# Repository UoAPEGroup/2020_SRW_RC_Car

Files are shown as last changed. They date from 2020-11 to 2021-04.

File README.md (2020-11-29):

# 2020 Summer Camp

- This repo contains work done by the students participating in the 2020 summer workshop, a voluntary summer internship program at UoA
- The students work on a project to design and build a wirelessly powered RC car
- The specifications for the design are (to be refined during the project)

| Parameter | Specification |
| --- | --- |
| Primary Supply | 50 V |
| IPT Frequency | 150 kHz |
| Rated Power | 50 W |
| Primary Compensation | LCL |
| Track Section Length | 1000 mm |
| Track Width | 300 mm |
| Lateral Tolerance | 50 mm |
| Max Change in k | 25% |
| Max Motor Voltage | 10 V |
| Max Steering Voltage | 5 V |
| Min Running Voltage  | 5 V |

- Work division is 
    - Power converter of the primary side IPT system: Sean McKeown & Henry Mitchell-Hibbert  
    - Embedded controller of the primary IPT system: Andrey Chukhraev & Isabelle Johns
    - Magnetic design of the primary side IPT coil: Arathi Biju & Alec Paton & Dexter Pham
    - Power converter of the vehicle side motor driver: Kimsong Lor  & Callum McDowell
    - Embedded controller of the vehicle side motor driver: Earlene Starling Babette & Raining Xing
    - Remote controller and steering controller of the vehicle: Neil Patil & Harris Tomy
    - Power converter of the vehicle side IPT system: Manoj Kumaraguru & Pranav Gulati

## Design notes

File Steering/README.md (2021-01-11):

# Design of the Remote and Steering Controllers

- Bluetooth Module 1R1 is located in `Steering/Hardware/Bluetooth_Module`
- Remote Controller 1R3 is located in `Steering/Hardware/Remote_Controller`
- Steering Converter 1R2 is located in `Steering/Hardware/Steering/Steering_Converter_1R2`

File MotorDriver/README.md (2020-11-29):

# Design of the Motor Driver

- Keep this document updated as you go

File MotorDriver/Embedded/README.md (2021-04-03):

# Motor Driver Embedded Side

The motor side embedded firmware controls the speed of the remote-controlled car by using PWM waves and an H-Bridge to variate the average voltage seen across the DC motor. Voltage at the H-Bridge, current at the H-Bridge, and motor power consumption data is sent to a live-updating website using BLE (bluetooth low energy) and an online PostGreSQL database. Safety features force the car to stop on over-voltage, over-current, and lost remote connection conditions.

## Features
- Uses an Atemga328PB to set the speed of the car between four set speeds [defined as STOP, MIN, MID, and MAX]
- Uses unipolar PWM modulation to change the duty cycle of PWM waves controlling the FETs in the H-Bridge
- Ramps voltage across motor at increments of 10 mV to prevent current spikes
- Switching frequency is 1.875kh
- Three safety paramaters cause the car to stop moving when triggered (at voltage > 20 V, current > 3 A, and if conenction to the remote controller team is lost)
- Connected to live-updating (voltage, current, and power data) website using BLE, python, and an online PostGreSQL database. See documentation here: link to software

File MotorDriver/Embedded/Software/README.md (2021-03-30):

# Live-updating Website

This website presents the H-Bridge voltage, H-Bridge current, and power through the wirelessly powered RC car through live-updating graphs. It also indicates the speed range (STOP, MIN, MID, MAX), direction (FORWARD, REVERSE), and which safety parameters (over voltage, over current, lost remote connection) are currently triggered.

website demo

## Features

* Graphs update live-time data relating to the voltage, current, and power of the car (speed is to be implemented)
* Indicates which safety parameter is triggered through button colors (red means that safety is triggered and that the car is stopped)
* Can be updated via bluetooth connection or serial connection to uController (note: serial connection is primarily used for testing)

## Documentation 

A local script (checkNearbyBLE.py) is used to find nearby BLE devices and print out their UUID numbers. 

The upstream script (updateDatabaseBL.py) reads incoming data from the microcontroller on the motor driver PCB. It then updates a PostGreSQL databse hosted on Heroku. This can be done sans bluetooth and with serial connection through (updateDatabseSerial.py).

A downstream script (bluetooth.py) periodically checks for updates in the databse. It generates the webpage and reflects any changes onto the graphs.

The webpage uses the Flask framework and is deployed via Heroku. 

## Key python libraries used: 

* Dash
* Plotly
* Bleak
* Psycopg2
* Asyncio
* Gunicorn
* Serial

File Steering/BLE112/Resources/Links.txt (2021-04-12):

BGSript VScode:
https://marketplace.visualstudio.com/items?itemName=SzczepanMejer.bgscript-support

https://www.digikey.com/eewiki/display/Wireless/Getting+Started+with+the+BlueGiga+BLE112+Bluetooth+Low+Energy+module
https://www.silabs.com/community/wireless/bluetooth/knowledge-base.entry.html/2015/08/06/_how-to_update_the-saZT

https://github.com/slackhappy/ble112/tree/master/serial_debug
https://sureshjoshi.com/embedded/bled112-virtual-com-stops-working/
https://github.com/CANBus-Triple/CBT-BLE112-Firmware
https://github.com/kilianc/iBeacon
https://github.com/sureshjoshi/ble113-firmware-examples

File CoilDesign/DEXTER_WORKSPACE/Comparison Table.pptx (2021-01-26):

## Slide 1

- # Ferrite Bars

- k_max (x = 0 mm, y = 50 mm)

- Minimum Power Output

- Maximum Power Output

- k_min (x = mid, y = 50 mm)

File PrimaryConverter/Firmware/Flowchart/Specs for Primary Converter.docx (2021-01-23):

Important specifications:

- System clock = 8MHz
- ADC resolution = 10-bit
- ADC clock = 250kHz
- ADC sampling every 1us using Timer/Counter1(16-bit) CTC comp_B (needs check)
- ADC sampling size = 10 readings per channel
- ADC reference voltage = AVCC = 3.3V
- USART0 – 8N1 – no parity
- Baud rate = 9600 (standard)
- Transmitting data to terminal every 1s using Timer/Counter3(16-bit) OVF
- Timer/Counter0, 2 are used for PWM signal generation to control the drivers for the H-bridge

Work in progress:

- Implementing ramping down of the PWM signals for over voltage, current and temperature
- Determining communication protocols with the Bluetooth module

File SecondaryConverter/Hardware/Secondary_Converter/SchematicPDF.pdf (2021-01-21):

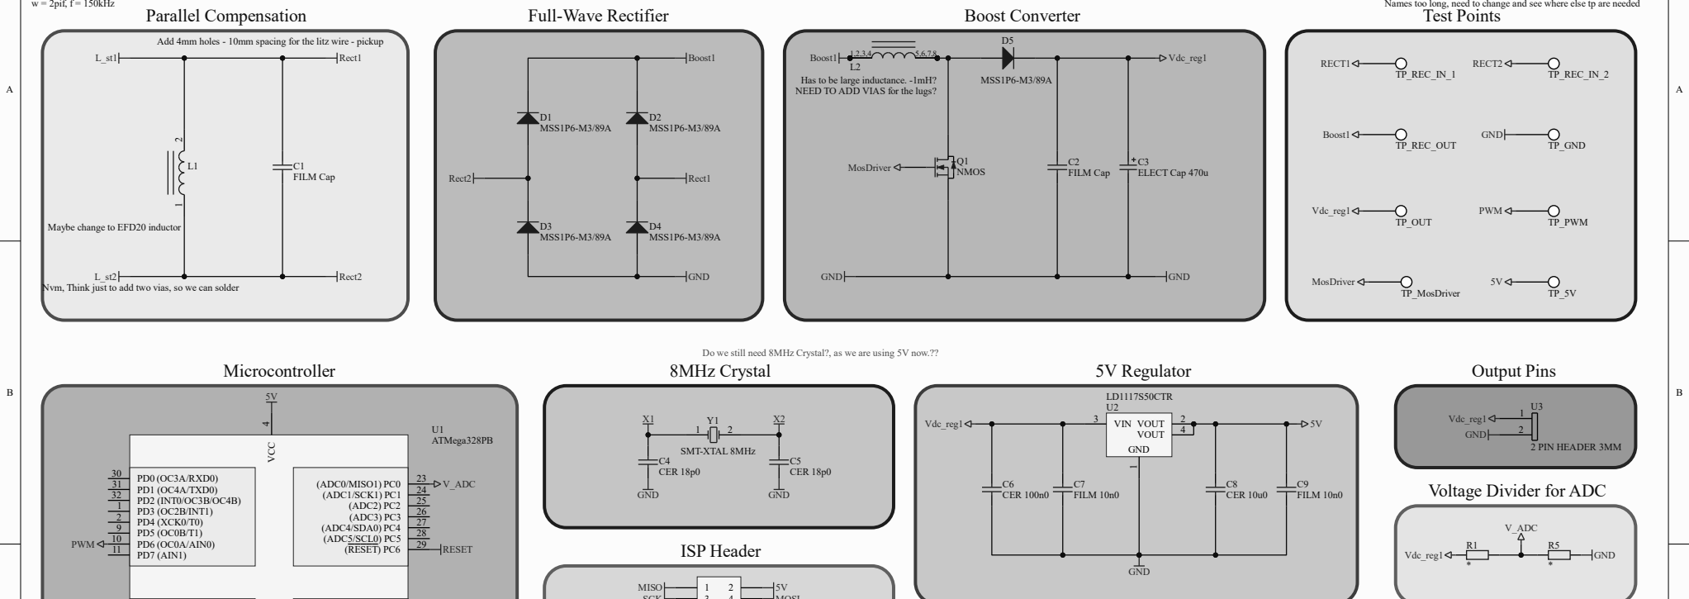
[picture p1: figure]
C1 FILM Cap; Rect1; Rect2; Parallel Compensation; D1 MSS1P6-M3/89A; D2 MSS1P6-M3/89A; D3 MSS1P6-M3/89A; D4 MSS1P6-M3/89A; Full-Wave Rectifier; Boost1; GND; MSS1P6-M3/89A; C2 FILM Cap; Vdc_reg1; Boost Converter 1 2; VCC; PD1 (OC4A/TXD0) 31 PD2 (INT0/OC3B/OC4B) 32 PD3 (OC2B/INT1) 1 PD4 (XCK0/T0) 2 PD5 (OC0B/T1) 9 PD6 (OC0A/AIN0) 10 PD7 (AIN1) 11; PD0 (OC3A/RXD0) 30; (ADC0/MISO1) PC0; (ADC1/SCK1) PC1; (ADC2) PC2; (ADC3) PC3; (ADC4/SDA0) PC4; (ADC5/SCL0) PC5; (RESET) PC6; U1 ATMega328PB; Q1 NMOS; NEED TO ADD VIAS for the lugs?; Has to be large inductance. -1mH?; TP_GND; TP_REC_IN_1; RECT1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
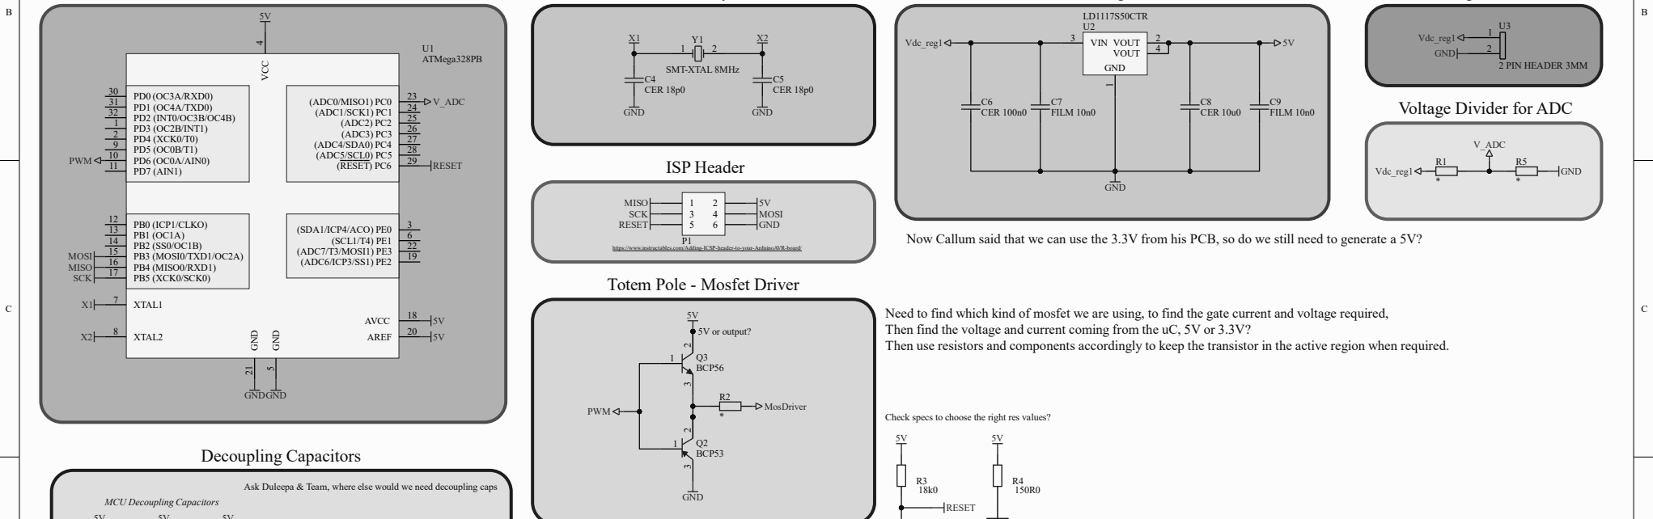
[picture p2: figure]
XTAL1 7; XTAL2 8; AVCC; AREF; PB5 (XCK0/SCK0) 17; PB0 (ICP1/CLKO) 12 PB1 (OC1A) 13 PB2 (SS0/OC1B) 14 PB3 (MOSI0/TXD1/OC2A) 15; PB4 (MISO0/RXD1) 16; (ADC6/ICP3/SS1) PE2; 19 (ADC7/T3/MOSI1) PE3; (SDA1/ICP4/ACO) PE0; (SCL1/T4) PE1; 6 GND; 5 GND 21; GNDGND; Decoupling Capacitors; SCK RESET; MOSI GND; https://www.instructables.com/Adding-ICSP-header-to-your-ArduinoAVR-board/; MISO SCK; MOSI; Q3 BCP56 2; Q2 BCP53; PWM; GND; 5V 5V or output?; MosDriver; Totem Pole - Mosfet Driver; MCU Decoupling Capacitors; RESET

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
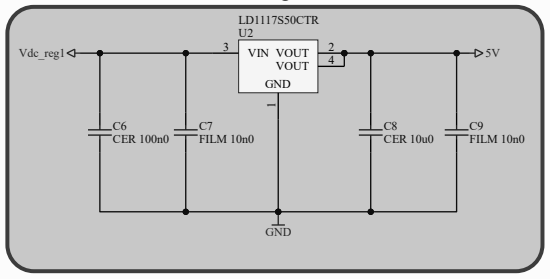
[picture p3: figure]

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
University Of Auckland
20 Symonds Street,
Auckland CBD,
Auckland 1010,

### 1 New Zealand

## Secondary Converter

1

21/01/2021 | 12:25:39 PM
C:\Users\Manoj\Documents\GitHub\2020-srw-rc-car\SecondaryConverter\Hardware\Secondary_Converter\IPT_Secondary_Converter.SchDoc

Title:

Author:
Date:
File:

Revision:
Time: | Sheet | of

### Pranav G & Manoj K

Note: Can only find the value of the capacitor after determing the value of the inducatnce As wL = 1/wC, C = 1/w^2*L
w = 2pif, f = 150kHz

Add 4mm holes - 10mm spacing for the litz wire - pickup

A Sinusoidal coil is used as the pick up, using parallel compensation to build the voltage and to achieve reasonance. Then the signal goes to the full-wave rectifier whcih transforms the ac voltage to dc voltage. The signal from the rectifiers goes to the boost converter.

Main Idea: As the pick up voltage is going to be a low AC voltage, need to convert this signal into a DC voltage and also boost up the voltage to 5-12V; ideally 10V.

Add regulator for 3v3/5v supply - possibly LD1117S50CTR . Add header for possible use by other teams. Add zener diode to protect regulator

# TO DO:

Do we still need 8MHz Crystal?, as we are using 5V now.??

C10
100n

C11
100n

C12
100n
GND | GND | GND
5V | 5V | 5V
C13
18n0

GND

GND

D6
Green

Input voltage in the range of 4-7V, maybe 3V, so for safety just keep it 3-8V. - Still need to confirm with Coil group

Now Callum said that we can use the 3.3V from his PCB, so do we still need to generate a 5V?

Need to find which kind of mosfet we are using, to find the gate current and voltage required,

## Then find the voltage and current coming from the uC, 5V or 3.3V?

Then use resistors and components accordingly to keep the transistor in the active region when required.

Ask Duleepa & Team, where else would we need decoupling caps

Check which type of diodes to use? Names too long, need to change and see where else tp are needed

Check specs to choose the right res values?

Nvm, Think just to add two vias, so we can solder

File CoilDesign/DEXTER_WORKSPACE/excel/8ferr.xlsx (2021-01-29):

Variation | $X_displacement | $Y_displacement | Lst_Wdg: Freq(150kHz): Matrix1 | k_Wdg: Freq(150kHz): Matrix1 | M_Wdg: Freq(150kHz): Matrix1 | L_pt_Wdg: Freq(150kHz): Matrix1
1 | 0mm | 0mm | 139.655626661595nH | 0.1221841069 | 216.627674501381nH | 22508.1603069312nH
2 | 0mm | 50mm | 139.491337467754nH | 0.08543539432 | 150.706136955698nH | 22306.8876871537nH
3 | 67.5mm | 0mm | 128.32776882356nH | 0.09409683698 | 159.205421658519nH | 22307.1975334523nH
4 | 67.5mm | 50mm | 128.399777350217nH | 0.06737563071 | 113.710914979nH | 22183.7187301038nH

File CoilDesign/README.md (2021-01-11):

# Design of the Primary and Secondary Couplers

FinalModel :
- Contains latest ansys model for project (no solution data to save space)

Analysis Results:
- Excel files exported from parametric sweep 3
- Graphs of k vs x and y displacement
- .xlsx file sheet 1 is password protected to avoid data corruption as sheet 2 is dependent on sheet 1 cell values
- password is abc123 (please do not change cell values without making backup)

- Update the .gitignore as needed to avoid storing solution files
- Keep this document updated as you go

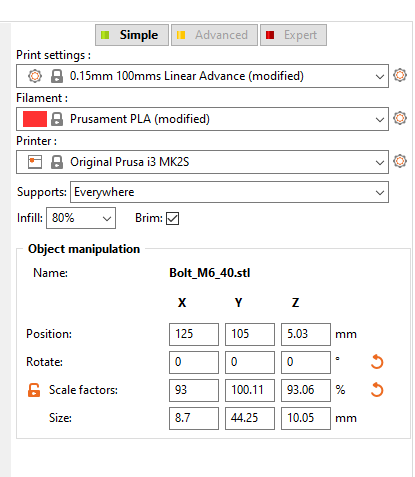
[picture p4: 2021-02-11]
CoilDesign/Arathi_Workspace/m6_40_settings.PNG

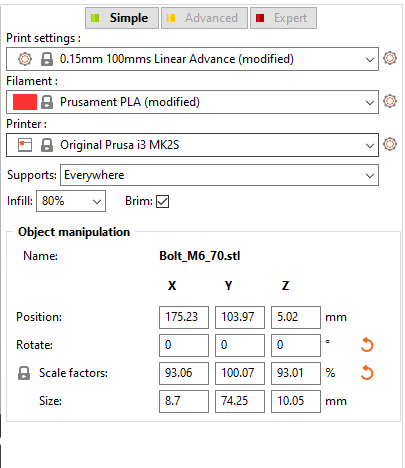
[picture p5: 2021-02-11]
CoilDesign/DEXTER_WORKSPACE/CONFIDENTIAL/m6_70_settings.PNG

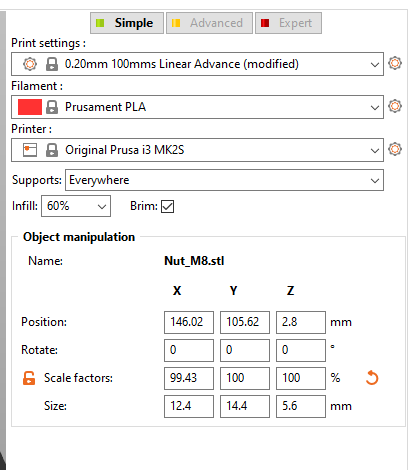
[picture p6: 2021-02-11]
CoilDesign/DEXTER_WORKSPACE/CONFIDENTIAL/m8_nut_settings.PNG

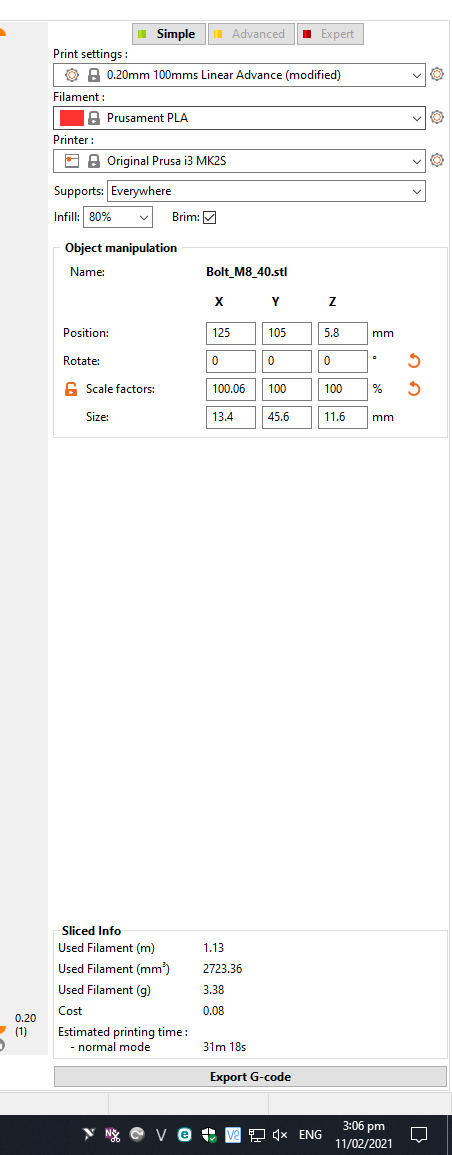
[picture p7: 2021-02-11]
CoilDesign/DEXTER_WORKSPACE/CONFIDENTIAL/m8_40_settings.PNG

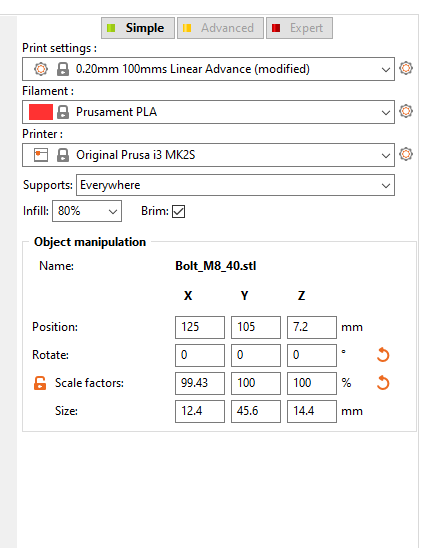
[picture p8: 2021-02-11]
CoilDesign/Arathi_Workspace/m8_40_settings.PNG

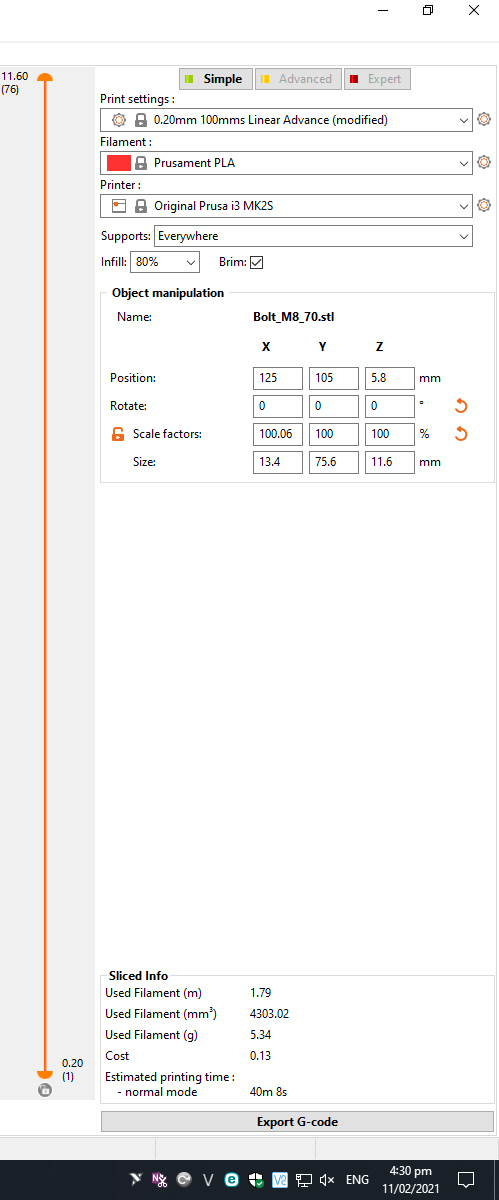
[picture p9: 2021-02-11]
CoilDesign/DEXTER_WORKSPACE/CONFIDENTIAL/m8_70_settings.PNG

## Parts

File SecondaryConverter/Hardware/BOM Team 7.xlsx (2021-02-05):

Index | Part Number | Supplier | Manufacturer Part Number | Description | QTY | QTY (Price Break) | Unit Cost (NZD) | Total Cost (NZD) | Unit PB Cost | Total PB Cost | Requester
1 | 445-7348-1-ND | Digikey | C1005X7R1E104K050BB | (Parallel Compensation) 0.1µF ±10% 25V Ceramic Capacitor X7R 0402 (1005 Metric) | 4 | 10 | 0.19 | 0.76 | 0.133 | 1.33 | Secondary
2 | SDT5H100P5-7DICT-ND | Digikey | SDT5H100P5 | Diode Schottky 100V 5A Surface Mount PowerDI™ 5 | 5 | 10 | 0.71 | 3.55 | 0.611 | 6.11 | Secondary
3 | BSC072N08NS5ATMA1CT-ND | Digikey | BSC072N08NS5ATMA1CT | N-Channel 80V 74A (Tc) 2.5W (Ta), 69W (Tc) Surface Mount PG-TDSON-8-7 | 1 | 10 | 2.72 | 2.72 | 2.228 | 22.28 | Secondary
4 | 1276-3387-1-ND | Digikey | CL32B106KBJNNNE | (Short-cct Reg Cap) 10µF ±10% 50V Ceramic Capacitor X7R 1210 (3225 Metric) | 1 | 10 | 0.88 | 0.88 | 0.623 | 6.23 | Secondary
5 | 36-5015CT-ND | Digikey | 5015 | PC Test Point, Miniature Phosphor Bronze, Silver Plating Surface Mount Mounting Type | 15 | 25 | 0.66 | 9.9 | 0.534 | 13.35 | Secondary & MotorDriver
6 | 1276-1003-1-ND | Digikey | CL21B104KBCNNNC | (Decoupling Caps) 0.1µF ±10% 50V Ceramic Capacitor X7R 0805 (2012 Metric) | 4 | 10 | 0.15 | 0.6 | 0.074 | 0.74 | Secondary
7 | 469-1027-ND | Digikey | 9027 | Magnet 1 | 3 | 5 | 0.62 | 1.86 | 0.592 | 2.96 | Raining
8 | 1835-M1219-1-ND | Digikey | M1219-1 | Magnet 2 | 3 | 5 | 0.89 | 3.89 | 0.852 | 4.26 | Raining
9 | AH374-W-7DICT-ND | Digikey | AH374-W-7 | Hall Effect Sensor | 3 | 10 | 1.02 | 3.06 | 0.89 | 8.9 | Raining
10 | 1470-4533-ND | Digikey | SRH05S12 | DC DC CONVERTER 12V | 2 | 5 | 12.34 | 24.68 | 11.972 | 59.86 | Primary
11 | 296-TMCS1100A3QDRCT-ND | Digikey | TMCS1100A3QDR | PRECISION ISOLATED CURRENT SENSOR | 3 | 10 | 6.5 | 19.5 | 5.83 | 58.3 | Primary
12 | 1470-2974-5-ND | Digikey | ISE0312A | DC DC CONVERTER 12V 1W | 1 | 5 | 6.79 | 6.79 | 6.36 | 31.8 | MotorDriver
13 | SMBJ5354B-TPMSCT-ND | Digikey | SMBJ5354B-TP | DIODE ZENER 17V 5W DO214AA | 1 | 10 | 0.63 | 0.63 | 0.544 | 5.44 | MotorDriver
14 | 1928-SMDTC04220TB00KQ00DKR-ND | Digkey | SMDTC04220TB00KQ00 | CAP FILM 2.2UF 10% 63VDC 2824 | 3 | 10 | 2.79 | 8.37 | 2.206 | 22.06 | MotorDriver
15 | 296-30207-ND | Digikey | CC-DEBUGGER | KIT DEBUGGER/PROGRAMMER | 1 | 1 | 90.72 | 90.72 | 90.72 | 90.72 | Duleepa <3
 |  |  |  |  |  |  |  | TOTAL PRICE (w/out PB) |  | TOTAL PRICE (w/ PB)
 |  |  |  |  |  |  |  | 177.91 |  | 334.34

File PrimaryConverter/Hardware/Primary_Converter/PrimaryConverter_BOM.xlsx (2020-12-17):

Steering Controller
Item # | Component | Description | Quantity | Price (Inc. GST) | Link | Notes
1 | EFD20/10/7-3C96 | FERRITE CORE | 4 | $1.45 | https://www.digikey.co.nz/product-detail/en/ferroxcube/EFD20-10-7-3C96/1779-1076-ND/7041536
2 | B66418W1008D001 | BOBBIN COIL FORMER EFD 20X10X7 | 2 | $2.31 | https://www.digikey.co.nz/product-detail/en/epcos-tdk-electronics/B66418W1008D001/495-5524-ND/3914936
3 | B66418B2000X000 | YOKE EFD 20 X 10 X 7 | 4 | $0.57 | https://www.digikey.co.nz/product-detail/en/epcos-tdk-electronics/B66418B2000X000/495-5523-ND/3915648
4 | BSC072N08NS5ATMA1 | MOSFET N-Ch 80V 74A TDSON-8 | 4 | $2.64 | https://nz.mouser.com/ProductDetail/Infineon-Technologies/BSC072N08NS5ATMA1/
5 | TMCS1100A2 | PRECISION ISOLATED CURRENT SENSOR | 1 | $3.98 | https://www.digikey.com/en/products/detail/texas-instruments/TMCS1100A2QDR/12696012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
6 | 8MHz Crystal | TXC CORP CRYSTAL 8.0000MHZ 18PF SMD | 1 | $0.67 | https://www.digikey.co.nz/product-detail/en/txc-corporation/9C-8-000MAAJ-T/887-1048-1-ND/2118925
7 | ATMEGA328PB-AU-ND | ATMEGA328PB-AU-ND | 1 | $1.34 | https://www.digikey.com/en/products/detail/microchip-technology/ATMEGA328PB-AU/5638812
8 | SRH05S12 | DC DC CONVERTER 12V | 1 | $12.79 | https://www.digikey.co.nz/products/en?keywords=srh05s12
9 | IRS21834SPBF | IC GATE DRVR HALF-BRIDGE 14SOIC | 2 | $4.83 | https://www.digikey.co.nz/product-detail/en/infineon-technologies/IRS21834SPBF/IRS21834SPBF-ND/1189739
10 | AP2210K-3.3TRG1 | IC REG LINEAR 3.3V 300MA SOT23-5 | 1 | $0.66 | https://www.digikey.co.nz/product-detail/en/diodes-incorporated/AP2210K-3-3TRG1/AP2210K-3-3TRG1DICT-ND/4505291
11 | MSS1P6-M3/89A | DIODE SCHOTTKY 60V 1A MICROSMP | 2 | $0.42 | https://www.digikey.co.nz/product-detail/en/vishay-semiconductor-diodes-division/MSS1P6-M3-89A/MSS1P6-M3-89AGICT-ND/2071763
12 | ECP-U1C104MA5 | CAP FILM 0.1UF 20% 16VDC 0805 | 7 | $0.91 | https://www.digikey.co.nz/product-detail/en/panasonic-electronic-components/ECP-U1C104MA5/PCF1126CT-ND/285453 | 0805 decoupling caps for 12V and down
13 | CGA5L2C0G1H104J160AA | CAP CER 0.1UF 50V C0G 1206 | 3 | $0.78 | https://www.digikey.co.nz/product-detail/en/tdk-corporation/CGA5L2C0G1H104J160AA/445-6984-1-ND/2673002 | 1206 decoupling caps for fet outer loop
14 | CL32B106KBJNNNE | CAP CER 10UF 50V X7R 1210 | 2 | $0.94 | https://www.digikey.co.nz/product-detail/en/samsung-electro-mechanics/CL32B106KBJNNNE/1276-3387-1-ND/3891473
15 | CL32B105KCJNNNE | CAP CER 1UF 100V X7R 1210 | 2 | $0.56 | https://www.digikey.co.nz/product-detail/en/samsung-electro-mechanics/CL32B105KCJNNNE/1276-1812-6-ND/3892326
16 | CL21B225KPFNNNE | CAP CER 2.2UF 10V X7R 0805 | 1 | $0.18 | https://www.digikey.co.nz/product-detail/en/samsung-electro-mechanics/CL21B225KPFNNNE/1276-1188-1-ND/3889274
17 | CL21B105KOFNNNG | CAP CER 1UF 16V X7R 0805 | 1 | $0.16 | https://www.digikey.co.nz/product-detail/en/samsung-electro-mechanics/CL21B105KOFNNNG/1276-6471-1-ND/5958099
18 | CL21C101JCANNNC | CAP CER 100PF 100V C0G/NP0 0805 | 1 | $0.16 | https://www.digikey.co.nz/product-detail/en/samsung-electro-mechanics/CL21C101JCANNNC/1276-1261-1-ND/3889347
19 | CL32B225KCJSNNE | CAP CER 2.2UF 100V X7R 1210 | 2 | $0.74 | https://www.digikey.co.nz/product-detail/en/samsung-electro-mechanics/CL32B225KCJSNNE/1276-3362-1-ND/3891448
20 | CL21C200JBANNNC | CAP CER 20PF 50V C0G/NP0 0805 | 2 | $0.16 | https://www.digikey.co.nz/product-detail/en/samsung-electro-mechanics/CL21C200JBANNNC/1276-1829-1-ND/3889915
21 | BLE112 | BLE112-A-V1C | 1 | $19.76 | https://www.digikey.co.nz/product-detail/en/silicon-labs/BLE112-A-V1C/336-4721-ND/7201185
22 | C2012C0G1V183J060AC | CAP CER 0.018UF 35V NP0 0805 | 6 | $0.34 | https://www.digikey.com/en/products/detail/tdk-corporation/C2012C0G1V183J060AC/6035663
23 | C2012C0G1H472J060AA | CAP CER 4700PF 50V C0G 0805 | 2 | $0.24 | https://www.digikey.com/en/products/detail/tdk-corporation/C2012C0G1H472J060AA/2732947
 |  | $0.42
 |  | $0.91
 |  | $0.78
 |  | $0.94
 |  | $0.56

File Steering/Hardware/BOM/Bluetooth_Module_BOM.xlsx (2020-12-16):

Bluetooth Module
Item # | Component | Description | Quantity | Price (Inc. GST) | Link | Total
1 | BLE112 | BLE112-A-V1C | 3 | $19.76 | https://www.digikey.co.nz/product-detail/en/silicon-labs/BLE112-A-V1C/336-4721-ND/7201185 | $59.28
2 | Ferrite Bead 1k at 100MHz | MFBM1V3216-102-R | 3 | $0.18 | https://www.digikey.co.nz/product-detail/en/eaton-electronics-division/MFBM1V3216-102-R/283-MFBM1V3216-102-RCT-ND/13161429 | $0.55
3 | Mini-USB Header | UJ2-MBH-1-SMT-TR | 3 | $0.90 | https://www.digikey.co.nz/product-detail/en/cui-devices/UJ2-MBH-1-SMT-TR/102-4003-1-ND/6187925 | $2.69
4 | 3V3 LDO | LDL1117S33R | 3 | $0.89 | https://www.digikey.co.nz/product-detail/en/stmicroelectronics/LDL1117S33R/497-17239-1-ND/7102079 | $2.66
5 | CAP CER 4.7UF 25V X7R 1206 | CL31B475KAHNNNE | 3 | $0.37 | https://www.digikey.co.nz/product-detail/en/samsung-electro-mechanics/CL31B475KAHNNNE/1276-1055-1-ND/3889141 | $1.10
6 | CAP CER 1UF 25V X7R 0805 | CL21B105KAFNNNE | 15 | $0.24 | https://www.digikey.co.nz/product-detail/en/samsung-electro-mechanics/CL21B105KAFNNNE/1276-1066-1-ND/3889152 | $3.62
7 | CAP CER 47PF 50V C0G/NP0 0805 | CL21C470JBANNNC | 6 | 0.184 | https://www.digikey.co.nz/product-detail/en/samsung-electro-mechanics/CL21C470JBANNNC/1276-1156-1-ND/3889242 | $1.10
8 | RES 33 OHM 0.5% 1/8W 0805 | ERA-6AHD330V | 6 | $0.18 | https://www.digikey.co.nz/product-detail/en/panasonic-electronic-components/ERA-6AHD330V/P123897CT-ND/9467826 | $1.10
9 | CRGCQ 0805 1K5 1% | CRGCQ0805F1K5 | 3 | 0.184 | https://www.digikey.co.nz/product-detail/en/te-connectivity-passive-product/CRGCQ0805F1K5/A129751CT-ND/8577583 | $0.55
 |  |  |  |  |  | $72.67

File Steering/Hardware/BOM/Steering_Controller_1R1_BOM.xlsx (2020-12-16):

Steering Controller 1R1
Item # | Component | Description | Quantity | Price (Inc. GST) | Link
1 | CAP CER 0.1UF 25V X7R 0805 | CL21B104KACNNNC | 10 | $0.18 | https://www.digikey.co.nz/product-detail/en/samsung-electro-mechanics/CL21B104KACNNNC/1276-1099-1-ND/3889185
2 | CAP CER 1UF 50V X5R 0805 | CL21A105KBCLNNC | 1 | $0.33 | https://www.digikey.co.nz/product-detail/en/samsung-electro-mechanics/CL21A105KBCLNNC/1276-2396-1-ND/3890482
3 | 18pF Capacitor | KEMET CAP CER 18PF 50V C0G/NP0 0805 | 2 | $0.20 | https://www.digikey.co.nz/product-detail/en/kemet/C0805C180K5GACTU/399-8030-1-ND/3471753
4 | 27k Resistor | Panasonic RES SMD 27K OHM 5% 1/2W 0805 | 1 | $0.18 | https://www.digikey.co.nz/product-detail/en/panasonic-electronic-components/ERJ-P06J273V/P27KADCT-ND/525489
5 | IC Motor | Diodes Incorporated ZXBM5210-S-13 | 1 | $2.00 | https://www.digikey.co.nz/product-detail/en/diodes-incorporated/ZXBM5210-S-13/ZXBM5210-S-13DIDKR-ND/4567816
6 | 8MHz Crystal | TXC CORP CRYSTAL 8.0000MHZ 18PF SMD | 1 | $0.67 | https://www.digikey.co.nz/product-detail/en/txc-corporation/9C-8-000MAAJ-T/887-1048-1-ND/2118925
7 | RES 10K OHM 1% 1/4W 0805 | RNCP0805FTD10K0 | 1 | $0.18 | https://www.digikey.co.nz/product-detail/en/stackpole-electronics-inc/RNCP0805FTD10K0/RNCP0805FTD10K0CT-ND/2240601
8 | IC Motor | Diodes Incorporated ZXBM5210-S-13 | 1 | $2.00 | https://www.digikey.co.nz/product-detail/en/diodes-incorporated/ZXBM5210-S-13/ZXBM5210-S-13DIDKR-ND/4567816
9 | ATMEGA328PB-AU-ND | ATMEGA328PB-AU-ND | 1 | $1.34 | https://www.digikey.com/en/products/detail/microchip-technology/ATMEGA328PB-AU/5638812

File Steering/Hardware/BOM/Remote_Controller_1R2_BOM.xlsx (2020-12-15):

Remote Controller 1R2
Item # | Description | Component | Quantity | Price (Inc. GST) | Link
1 | 3V3 LDO Regulator | LDL1117S33R | 1 | $0.89 | https://www.digikey.co.nz/product-detail/en/stmicroelectronics/LDL1117S33R/497-17239-1-ND/7102079
2 | CAP CER 4.7UF 25V X7R 1210 | CL32B475KBUYNNE | 1 | $0.76 | https://www.digikey.co.nz/product-detail/en/samsung-electro-mechanics/CL32B475KBUYNNE/1276-1292-1-ND/3889378
3 | CAP CER 1UF 50V X5R 0805 | CL21A105KBCLNNC | 1 | $0.33 | https://www.digikey.co.nz/product-detail/en/samsung-electro-mechanics/CL21A105KBCLNNC/1276-2396-1-ND/3890482
4 | DIODE GEN PURP 75V 500MA SOD123 | CDSW4448-G | 1 | $0.40 | https://www.digikey.co.nz/product-detail/en/comchip-technology/CDSW4448-G/641-2069-1-ND/10131655
5 | CAP CER 1UF 25V X7R 0805 | CL21B105KAFNNNE | 6 | $0.24 | https://www.digikey.co.nz/product-detail/en/samsung-electro-mechanics/CL21B105KAFNNNE/1276-1066-1-ND/3889152
6 | 8MHz Crystal | TXC CORP CRYSTAL 8.0000MHZ 18PF SMD | 1 | $0.67 | https://www.digikey.co.nz/product-detail/en/txc-corporation/9C-8-000MAAJ-T/887-1048-1-ND/2118925
7 | 18pF Capacitor | KEMET CAP CER 18PF 50V C0G/NP0 0805 | 2 | $0.20 | https://www.digikey.co.nz/product-detail/en/kemet/C0805C180K5GACTU/399-8030-1-ND/3471753
8 | RES SMD 220 OHM 5% 0.4W 0805 | RHM220KCT-ND | 1 | $0.18 | https://www.digikey.co.nz/product-detail/en/rohm-semiconductor/ESR10EZPJ221/RHM220KCT-ND/1762990
9 | CAP CER 0.1UF 25V X7R 0805 | CL21B104KACNNNC | 4 | $0.18 | https://www.digikey.co.nz/product-detail/en/samsung-electro-mechanics/CL21B104KACNNNC/1276-1099-1-ND/3889185
10 | RES 10K OHM 1% 1/4W 0805 | RNCP0805FTD10K0 | 5 | $0.18 | https://www.digikey.co.nz/product-detail/en/stackpole-electronics-inc/RNCP0805FTD10K0/RNCP0805FTD10K0CT-ND/2240601
11 | RES SMD 27K OHM 5% 1/2W 0805 | ERJ-P06J273V | 1 | $0.18 | https://www.digikey.co.nz/product-detail/en/panasonic-electronic-components/ERJ-P06J273V/P27KADCT-ND/525489
12 | RES 1K OHM 1% 1/4W 0805 | RNCP0805FTD1K00 | 6 | $0.18 | https://www.digikey.co.nz/product-detail/en/stackpole-electronics-inc/RNCP0805FTD1K00/RNCP0805FTD1K00CT-ND/2240568

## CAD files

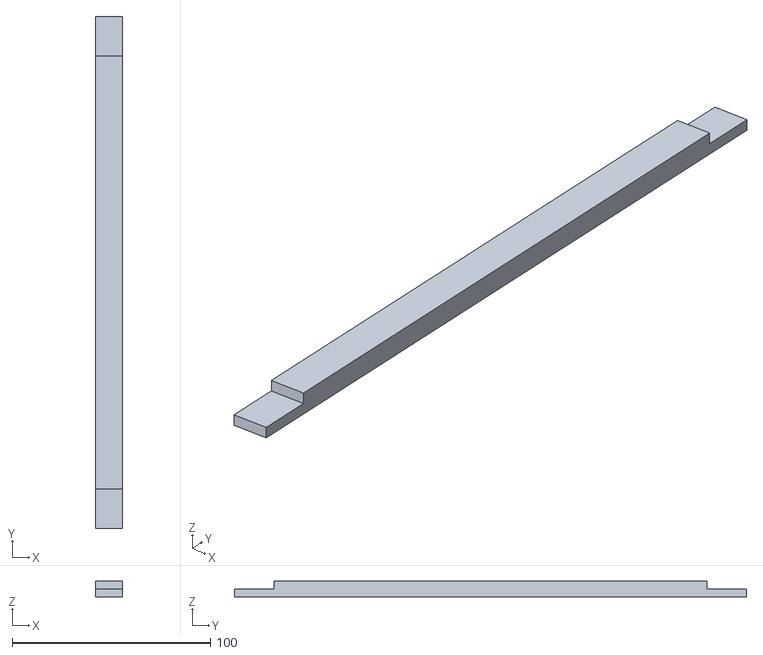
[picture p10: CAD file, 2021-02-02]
CoilDesign/DEXTER_WORKSPACE/CAD stuff/Final_CAD/recycle bin/spacer_no_wireholder.stl
13.5 x 258.0 x 8.00

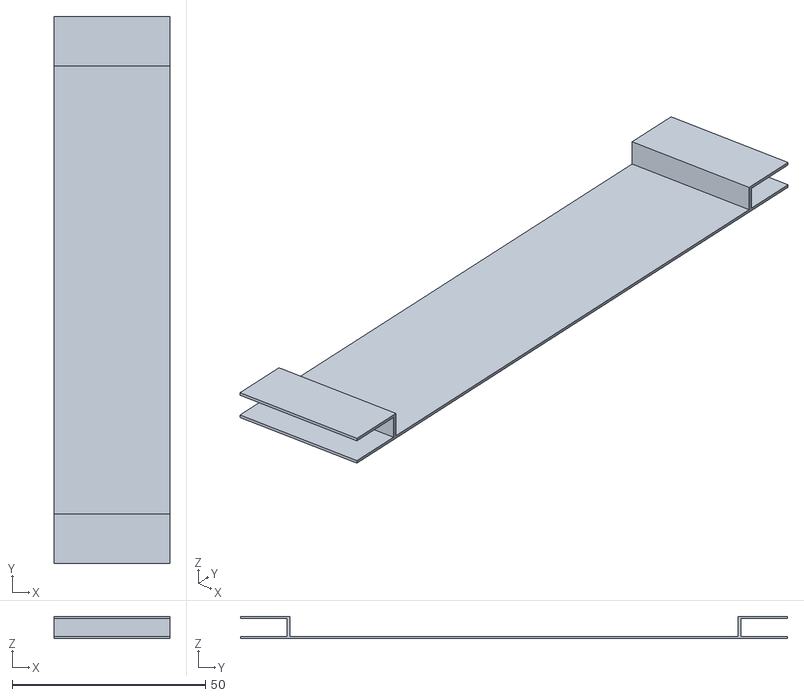
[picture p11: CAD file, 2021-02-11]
CoilDesign/DEXTER_WORKSPACE/CAD stuff/pduy110_coil_spacer.stl
30.0 x 141.6 x 5.80

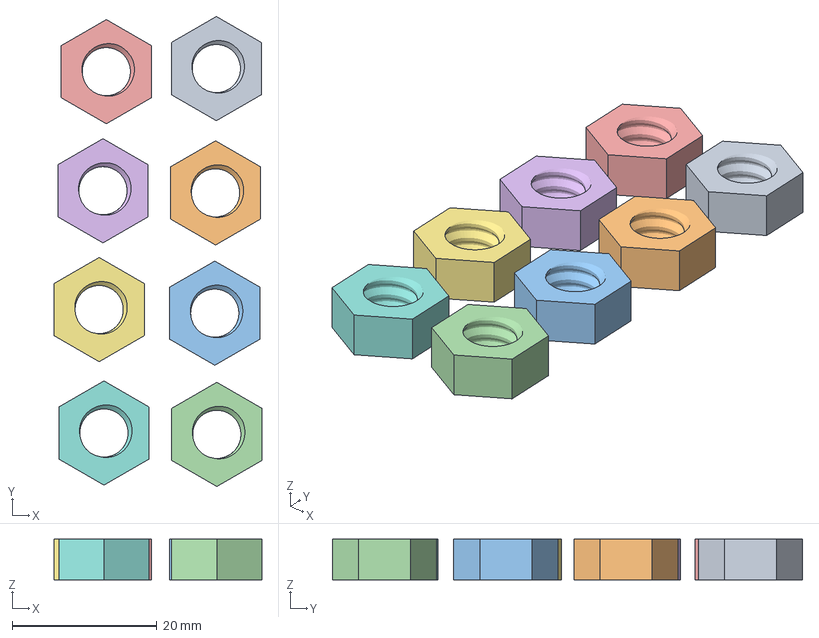
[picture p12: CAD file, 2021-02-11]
CoilDesign/DEXTER_WORKSPACE/stl folder/pduy110_8xNuts_M8_40_60inflat_0.2mm.3mf
28.7 x 64.9 x 5.60 mm
Nut_M8.stl x 8

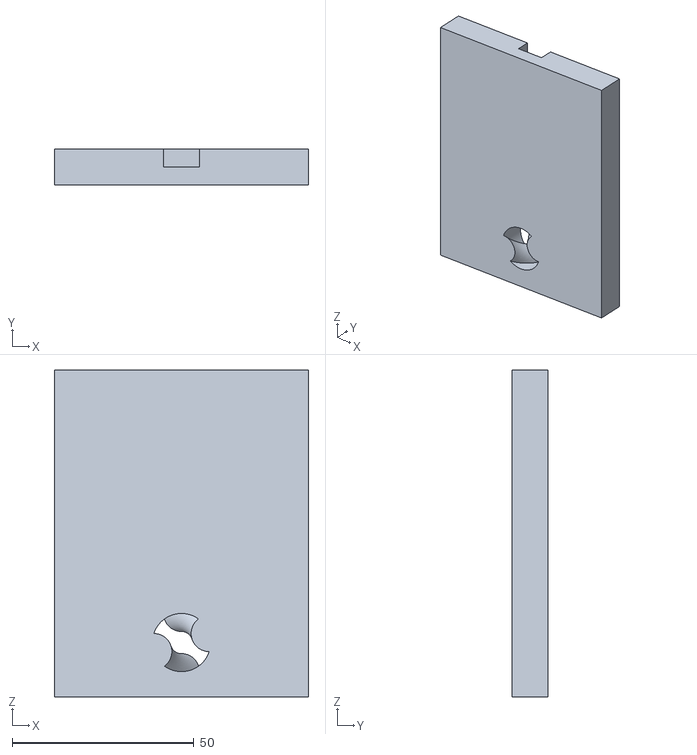
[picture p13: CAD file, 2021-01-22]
PrimaryConverter/Firmware/Kimsong_qi_coil/Part3.stl
70.0 x 10.0 x 90.0

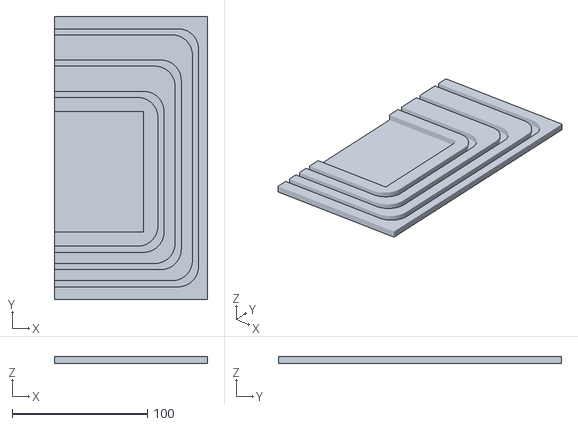
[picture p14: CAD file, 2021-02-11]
CoilDesign/Arathi_Workspace/pduy110_test_wireholder_coil.stl
113.1 x 209.6 x 4.95

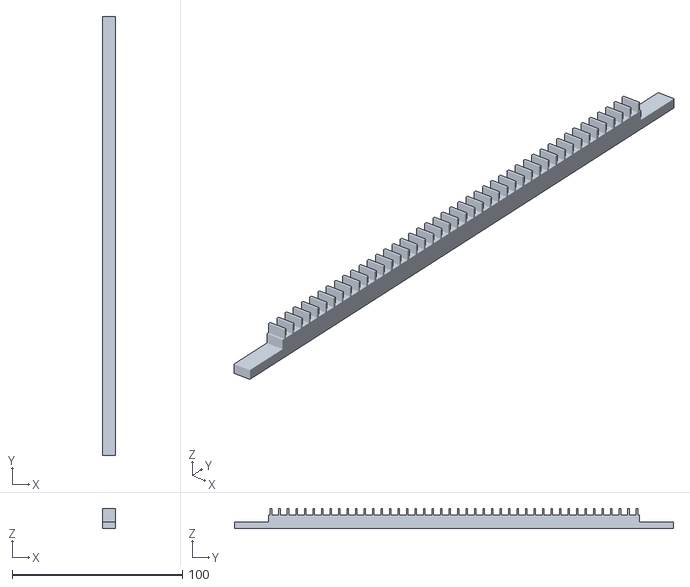
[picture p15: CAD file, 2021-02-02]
CoilDesign/DEXTER_WORKSPACE/CAD stuff/Final_CAD/recycle bin/spacer_wireholder_7.5mm_prototype_0R2.stl
7.50 x 258.0 x 12.0

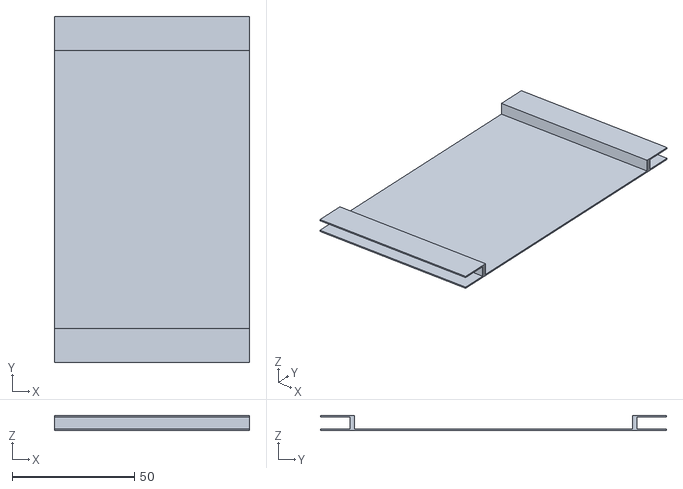
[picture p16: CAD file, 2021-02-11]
CoilDesign/DEXTER_WORKSPACE/CAD stuff/testcoil_spacer.stl
80.0 x 141.6 x 5.95

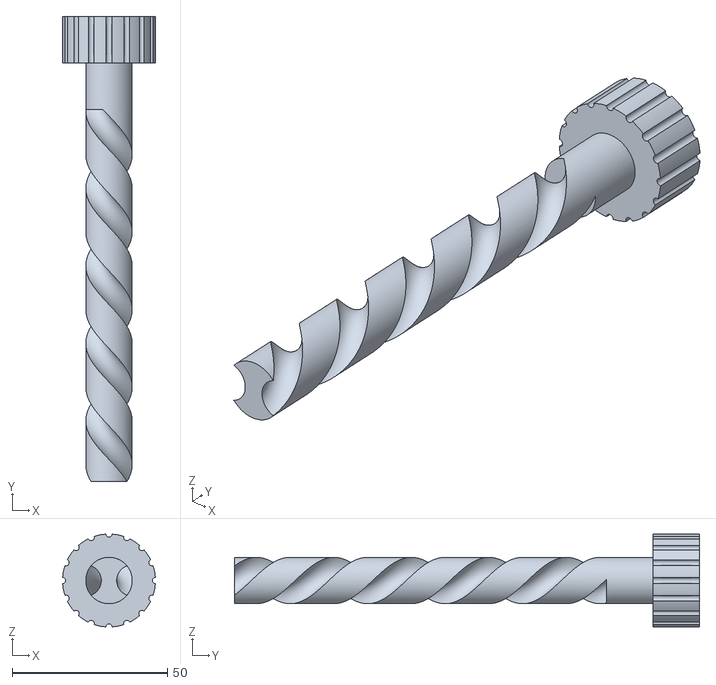
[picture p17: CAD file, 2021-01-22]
PrimaryConverter/Firmware/Kimsong_qi_coil/Part1_mod.stl
29.9 x 150.0 x 29.9

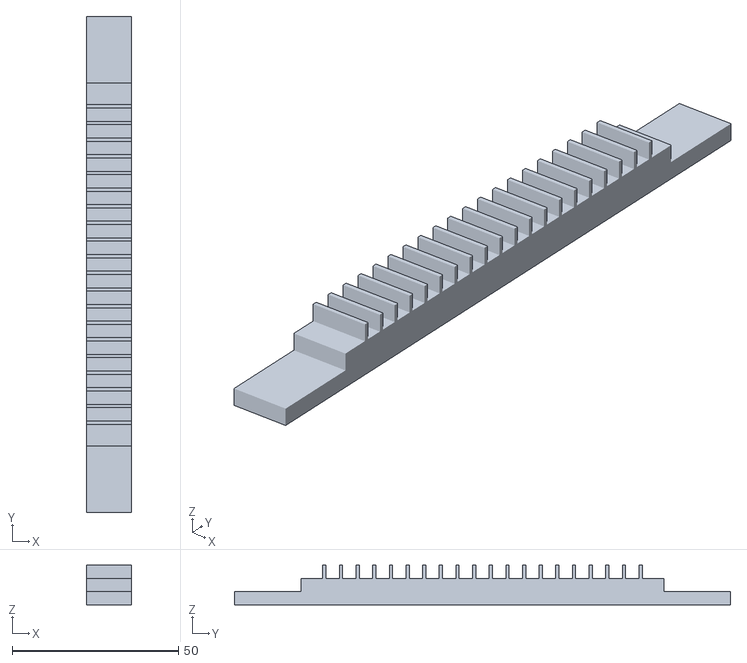
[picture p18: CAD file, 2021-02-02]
CoilDesign/DEXTER_WORKSPACE/CAD stuff/Final_CAD/recycle bin/spacer_0R2_beta.stl
13.5 x 149.0 x 12.0

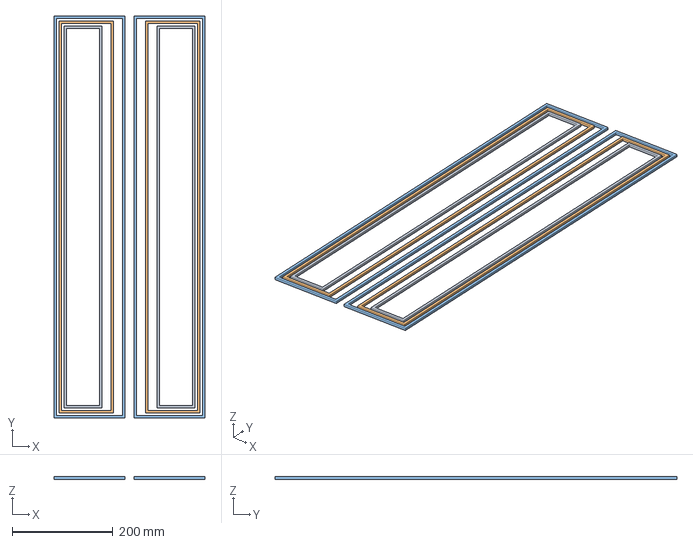
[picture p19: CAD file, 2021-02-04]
CoilDesign/DEXTER_WORKSPACE/CAD stuff/primary_coil_0R1_800mm.stp
300.0 x 800.0 x 5.00 mm

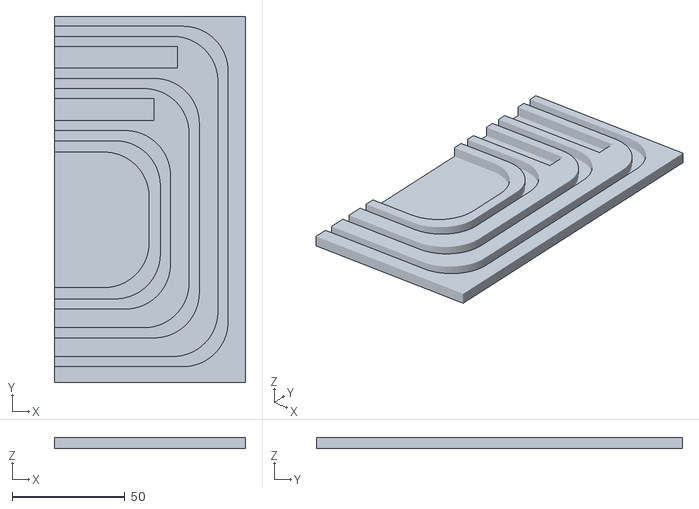
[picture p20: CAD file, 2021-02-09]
CoilDesign/DEXTER_WORKSPACE/stl folder/pduy110_primary_coil_0R2_test_cut_4.5mm_20mm.stl
84.8 x 162.0 x 4.95

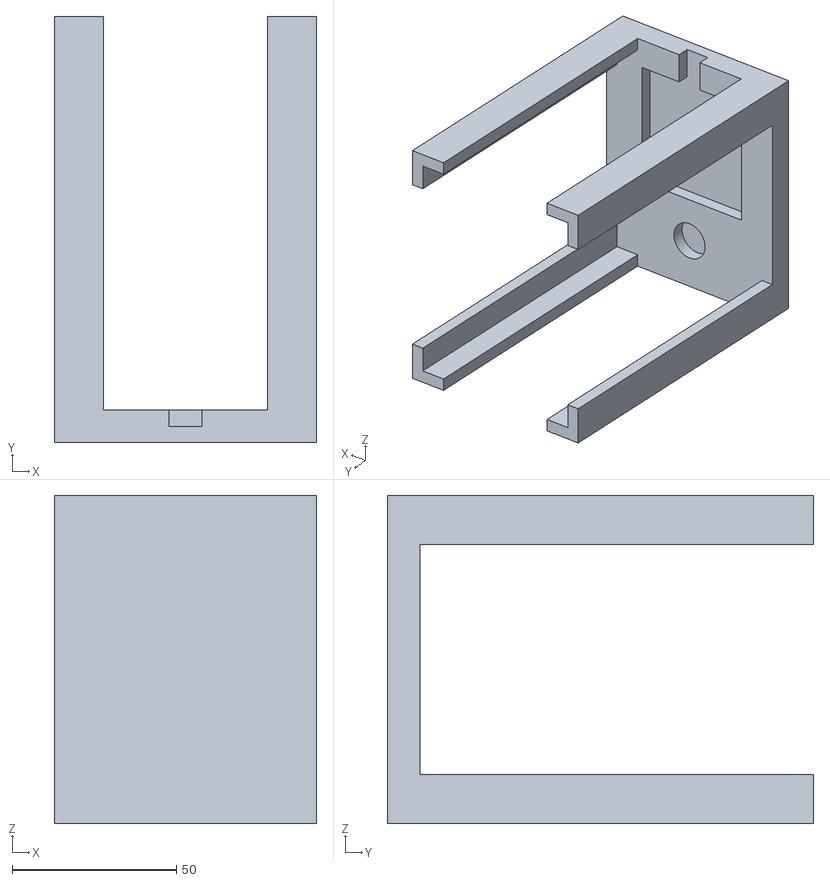
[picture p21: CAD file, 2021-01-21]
PrimaryConverter/Firmware/Kimsong_qi_coil/Part2.stl
80.0 x 130.0 x 100.0

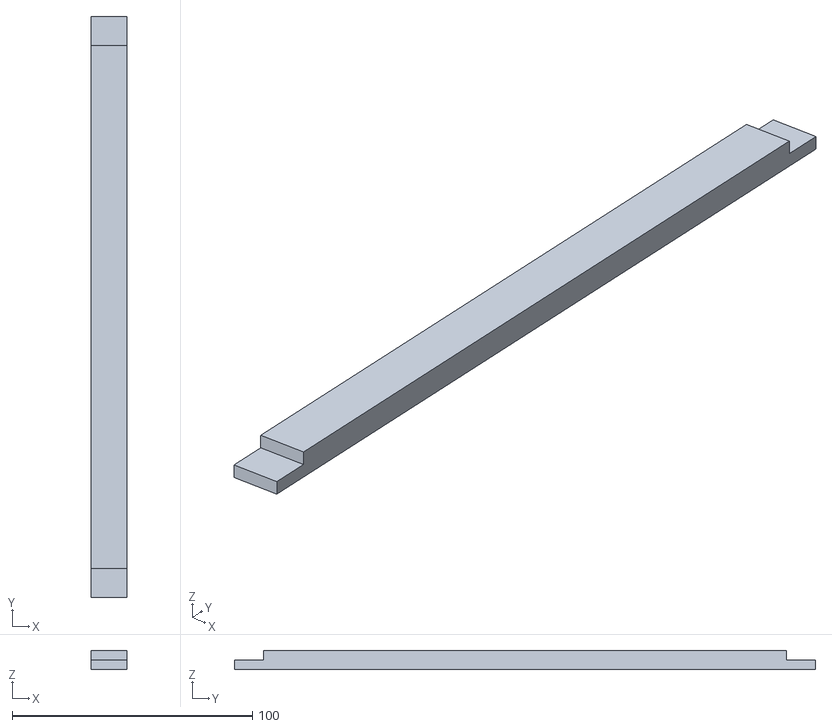
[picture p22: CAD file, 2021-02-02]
CoilDesign/DEXTER_WORKSPACE/CAD stuff/Final_CAD/recycle bin/spacer.stl
15.0 x 242.0 x 8.00

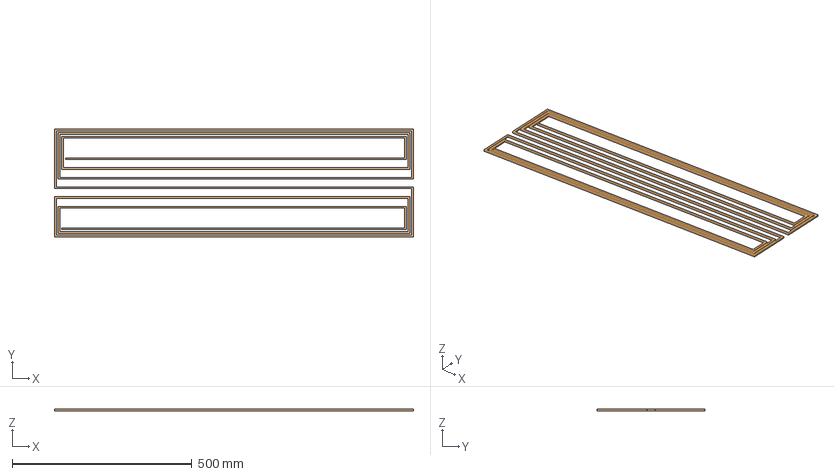
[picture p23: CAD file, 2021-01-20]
CoilDesign/DEXTER_WORKSPACE/CAD stuff/primary_coil_0R2.stp
1000.0 x 300.0 x 5.00 mm

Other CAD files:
CoilDesign/CAD Track/Wire Cad Model/wire_half.dwg
CoilDesign/CAD Track/Wire Cad Model/wire_drawing.dwg
CoilDesign/DEXTER_WORKSPACE/stl folder/pduy110_primary_coil_0R2_test_cut_4.5mm_15_innter_18.5_outer.stl
CoilDesign/Arathi_Workspace/400mmWireHolesFerriteLayer.idw
CoilDesign/Arathi_Workspace/500mmWireHolesFerriteLayer.idw
CoilDesign/Arathi_Workspace/Bolt_M6_40.stl
CoilDesign/Arathi_Workspace/Bolt_M6_70.stl
CoilDesign/Arathi_Workspace/Bolt_M8_40.stl
CoilDesign/Arathi_Workspace/Nut_M8.stl
CoilDesign/Arathi_Workspace/OldVersions/WireHolesFerriteLayer.0001.idw
CoilDesign/Arathi_Workspace/OldVersions/ferrite_layer_dex_1R1.0006.ipt
CoilDesign/Arathi_Workspace/WireHolesFerriteLayer.idw
CoilDesign/Arathi_Workspace/ferrite_layer_dex_1R1.idw
CoilDesign/Arathi_Workspace/primary_coil_0R2.ipt
CoilDesign/CAD Track/Assembly1.iam
CoilDesign/CAD Track/Assembly_final.iam
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

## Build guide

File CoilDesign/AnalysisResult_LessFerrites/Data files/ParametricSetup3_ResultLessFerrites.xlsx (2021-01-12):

Variation | $X_displacement | $Y_displacement | Lpt_new: Freq(150kHz): None | L_st: Freq(150kHz): None | k_new: Freq(150kHz): None | Mpt_st: Freq(150kHz): None | VA_pt: Freq(150kHz): None
1 | 70mm | 0mm | 2641.26774032865nH | 126.69323236254nH | 0.0972481202 | 56.2553896316643nH | 995734479501.625nH
2 | 70mm | 5mm | 2645.43163824834nH | 126.949634680969nH | 0.09698324939 | 56.203159474698nH | 997304232035.401nH
3 | 70mm | 10mm | 2643.84027172096nH | 126.757639363725nH | 0.09547410802 | 55.2701047531053nH | 996704300988.41nH
4 | 70mm | 15mm | 2643.00521736221nH | 126.846694864481nH | 0.09318894633 | 53.9576453510575nH | 996389492911.753nH
5 | 70mm | 20mm | 2640.6721996777nH | 126.754098081898nH | 0.09011276908 | 52.1344248477033nH | 995509965965.551nH
6 | 70mm | 25mm | 2642.30201875463nH | 127.163690860016nH | 0.086332421 | 50.043388711353nH | 996124393282.204nH
7 | 70mm | 30mm | 2636.74176028584nH | 126.860332982007nH | 0.08156749159 | 47.1752085872818nH | 994028225223.29nH
8 | 70mm | 35mm | 2632.37132180756nH | 126.75913437314nH | 0.07608440196 | 43.9499959171786nH | 992380608733.329nH
9 | 70mm | 40mm | 2629.82476036765nH | 126.708426109156nH | 0.07010860489 | 40.4703982667931nH | 991420577687.946nH
10 | 70mm | 45mm | 2629.86480580756nH | 126.809763005208nH | 0.06342444506 | 36.6268637598182nH | 991435674463.126nH
11 | 70mm | 50mm | 2622.04597928728nH | 126.563385318979nH | 0.05629706356 | 32.4309697922572nH | 988488046308.43nH
12 | 60mm | 0mm | 2645.54497850287nH | 127.32937714895nH | 0.09996605387 | 58.0195599993347nH | 997346960304.719nH
13 | 60mm | 5mm | 2648.90247213439nH | 127.338476969643nH | 0.09932668289 | 57.6871046423117nH | 998612705583.989nH
14 | 60mm | 10mm | 2643.11570123043nH | 127.081634242213nH | 0.09794099665 | 56.7628250598663nH | 996431144348.802nH
15 | 60mm | 15mm | 2644.27713942911nH | 127.258478608892nH | 0.09569465353 | 55.5116994361258nH | 996868996234.312nH
16 | 60mm | 20mm | 2639.84712035961nH | 127.212473850028nH | 0.09235832461 | 53.5217473465809nH | 995198918390.629nH
17 | 60mm | 25mm | 2641.08993803336nH | 127.321643150173nH | 0.08837726742 | 51.2487505817917nH | 995667449615.464nH
18 | 60mm | 30mm | 2632.70452488153nH | 126.895916714242nH | 0.08339398575 | 48.201395824714nH | 992506223332.849nH
19 | 60mm | 35mm | 2634.180839153nH | 127.291217233853nH | 0.07799398673 | 45.1630364496868nH | 993062780701.208nH
20 | 60mm | 40mm | 2625.0711496563nH | 126.857142885206nH | 0.0714651981 | 41.2403748704543nH | 989628508669.288nH
21 | 60mm | 45mm | 2626.74804498121nH | 127.232679726137nH | 0.06482299908 | 37.4746569623218nH | 990260683313.318nH
22 | 60mm | 50mm | 2625.27809628356nH | 127.087392009404nH | 0.05762940586 | 33.2876421077372nH | 989706525709.754nH
23 | 50mm | 0mm | 2648.46947155296nH | 127.940110018579nH | 0.1045763524 | 60.8743497726943nH | 998449468210.513nH
24 | 50mm | 5mm | 2644.33575072054nH | 127.79845018432nH | 0.1039748993 | 60.4434994209665nH | 996891092170.619nH
25 | 50mm | 10mm | 2646.79398421528nH | 128.116945779304nH | 0.102549886 | 59.7170766725738nH | 997817824365.165nH
26 | 50mm | 15mm | 2645.36177053507nH | 128.103997355213nH | 0.09997376074 | 58.1982474521558nH | 997277892528.031nH
27 | 50mm | 20mm | 2642.43391612179nH | 127.921482491173nH | 0.09658129335 | 56.152206465464nH | 996174117418.168nH
28 | 50mm | 25mm | 2641.31547529705nH | 128.158634653743nH | 0.09230985157 | 53.7071524295761nH | 995752475160.749nH
29 | 50mm | 30mm | 2633.37411038601nH | 127.727822542175nH | 0.08711110642 | 50.5210728915935nH | 992758651121.069nH
30 | 50mm | 35mm | 2634.66671551017nH | 127.882804117482nH | 0.0812291679 | 47.1499158695991nH | 993245951772.517nH
31 | 50mm | 40mm | 2629.48718111697nH | 127.887558842366nH | 0.07476564051 | 43.3562524065828nH | 991293313308.674nH
32 | 50mm | 45mm | 2630.79419838861nH | 128.011727956809nH | 0.06743798827 | 39.1356835929206nH | 991786047211.719nH
33 | 50mm | 50mm | 2626.45839310413nH | 128.199305487192nH | 0.05990745057 | 34.7623347190158nH | 990151487128.224nH
34 | 40mm | 0mm | 2656.89283735505nH | 129.779638175852nH | 0.1117877563 | 65.6424131042655nH | 1001625002305.2nH
35 | 40mm | 5mm | 2652.47259070967nH | 129.627441741572nH | 0.1110904635 | 65.1404427502183nH | 999958608578.615nH
36 | 40mm | 10mm | 2655.82112972796nH | 130.005898409771nH | 0.1096104441 | 64.4069712039598nH | 1001220978048.23nH
37 | 40mm | 15mm | 2648.2376763308nH | 129.56415884578nH | 0.1067692299 | 62.5413181434214nH | 998362083470.466nH
38 | 40mm | 20mm | 2649.62678998651nH | 129.650761706354nH | 0.1030441149 | 60.3952916403865nH | 998885766981.16nH
39 | 40mm | 25mm | 2648.31330882642nH | 129.76307388319nH | 0.09844813166 | 57.7122122838646nH | 998390596249.579nH
40 | 40mm | 30mm | 2643.70539313483nH | 129.75837715796nH | 0.09304983668 | 54.4991647515415nH | 996653452959.372nH
41 | 40mm | 35mm | 2638.82552928531nH | 129.502578375602nH | 0.08660669365 | 50.6286101282864nH | 994813787628.951nH
42 | 40mm | 40mm | 2635.92332172903nH | 129.718333820157nH | 0.07964893746 | 46.5743769381344nH | 993719681156.39nH
43 | 40mm | 45mm | 2624.3925844309nH | 129.186600406362nH | 0.07152098684 | 41.6444023740186nH | 989372695606.038nH
44 | 40mm | 50mm | 2632.4893648378nH | 129.759393820657nH | 0.06350175871 | 37.114060391778nH | 992425109907.323nH
45 | 30mm | 0mm | 2660.18075308241nH | 132.327366480517nH | 0.1216253977 | 72.1613553370168nH | 1002864517332.56nH
46 | 30mm | 5mm | 2661.88116675906nH | 132.445709614962nH | 0.1209207172 | 71.7982722120317nH | 1003505558186.32nH
47 | 30mm | 10mm | 2659.20120365605nH | 132.359539355061nH | 0.119052982 | 70.6306984132924nH | 1002495235898.76nH
48 | 30mm | 15mm | 2658.5031182458nH | 132.486409726408nH | 0.1161325091 | 68.9220302095629nH | 1002232063899.19nH
49 | 30mm | 20mm | 2653.34614251108nH | 132.431170852449nH | 0.1119867487 | 66.3832789488101nH | 1000287929849.24nH
50 | 30mm | 25mm | 2650.67664584825nH | 132.077336569955nH | 0.1068569433 | 63.2259369672316nH | 999281553316.669nH
51 | 30mm | 30mm | 2642.70351806462nH | 132.135927389975nH | 0.1008256608 | 59.5807213318368nH | 996275754956.124nH
52 | 30mm | 35mm | 2648.99799603448nH | 132.704261361003nH | 0.09396346 | 55.711166215004nH | 998648717245.921nH
53 | 30mm | 40mm | 2644.8757861852nH | 132.577297636919nH | 0.08609247371 | 50.9803025127375nH | 997094680744.436nH
54 | 30mm | 45mm | 2636.23177657568nH | 132.156817991773nH | 0.0773919262 | 45.6806461047066nH | 993835965894.014nH
55 | 30mm | 50mm | 2630.28993100567nH | 132.158343523154nH | 0.06821879306 | 40.2210251802469nH | 991595942887.035nH
56 | 20mm | 0mm | 2674.02697479563nH | 136.680591131114nH | 0.1337395311 | 80.8529951084222nH | 1008084419942.27nH
57 | 20mm | 5mm | 2669.82825896518nH | 136.469078441424nH | 0.1329918423 | 80.2756432864391nH | 1006501541365.37nH
58 | 20mm | 10mm | 2671.95219086028nH | 136.729131488069nH | 0.1309614232 | 79.1568047269841nH | 1007302244825.98nH
59 | 20mm | 15mm | 2666.21887428239nH | 136.606976100488nH | 0.1277751203 | 77.1135393295688nH | 1005140835396.96nH
60 | 20mm | 20mm | 2665.95367873725nH | 136.775701669789nH | 0.1232005171 | 74.394924294149nH | 1005040859031.8nH
61 | 20mm | 25mm | 2661.04286290414nH | 136.70203537835nH | 0.1175438581 | 70.8946343177979nH | 1003189525078.46nH
62 | 20mm | 30mm | 2656.41318712474nH | 136.656483127811nH | 0.1108352545 | 66.7791453226979nH | 1001444178428.41nH
63 | 20mm | 35mm | 2650.15806173958nH | 136.916040442311nH | 0.103086257 | 62.0960285468836nH | 999086051713.542nH
64 | 20mm | 40mm | 2646.96473242865nH | 136.875154001584nH | 0.09426544967 | 56.7399477342599nH | 997882194925.095nH
65 | 20mm | 45mm | 2644.46594760052nH | 136.644199666906nH | 0.08453873243 | 50.8183221405793nH | 996940175238.018nH
66 | 20mm | 50mm | 2638.10066278644nH | 136.556505669056nH | 0.07423539028 | 44.5566853260298nH | 994540519396.831nH
67 | 10mm | 0mm | 2680.13817500752nH | 141.303896066781nH | 0.1452878475 | 89.4097643205354nH | 1010388288145.1nH
68 | 10mm | 5mm | 2680.84070358297nH | 141.559180177797nH | 0.1445394483 | 89.0411820144387nH | 1010653135178.49nH
69 | 10mm | 10mm | 2680.94993382513nH | 141.755131366488nH | 0.1425289744 | 87.8652008708969nH | 1010694314009.65nH
70 | 10mm | 15mm | 2680.9360469312nH | 141.721314193528nH | 0.138814149 | 85.5646833576473nH | 1010689078773.97nH

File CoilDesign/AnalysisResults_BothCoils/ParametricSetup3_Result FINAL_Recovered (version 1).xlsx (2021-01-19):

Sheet: ydisp
 | N1 | 3 |  | I1 | 5 |  |  | f | 150000 | Q_2 | 5
 | N2 | 5 |  | I2 | 0 |  |  | w | 942477.7961
Xdisp | ydisp | Lpt_new (nH) | L_st (nH) | k_new (nH) | Mpt_st (nH) | VA_pt (VA) | VA_st (VA) | Po(W) | Vst |  | L_1 | L_2 | M_12 | k | Voc | Isc | Su | P_out | V_L_1 | VA_1
0 | 0 | 3033.738968 | 129.2205845 | 0.118156151 | 73.97948309 | 71.48079041 | 0 | 0 | 0.3486201009 |  | 27.30365071 | 3.230514613 | 1.109692246 | 0.1181561515 | 5.229301513 | 1.717516216 | 8.981410145 | 44.90705073 | 128.6654227 | 643.3271137
0 | 5 | 3033.548947 | 129.2766292 | 0.117538141 | 73.60618851 | 71.47631316 | 0 | 0 | 0.3468609916 |  | 27.30194053 | 3.23191573 | 1.104092828 | 0.1175381407 | 5.202914874 | 1.708108936 | 8.887145389 | 44.43572695 | 128.6573637 | 643.2868184
0 | 10 | 3030.610997 | 129.1327618 | 0.115787974 | 72.43471768 | 71.40708933 | 0 | 0 | 0.3413405654 |  | 27.27549897 | 3.228319045 | 1.086520765 | 0.1157879739 | 5.120108481 | 1.682796449 | 8.616100371 | 43.08050186 | 128.5327608 | 642.6638039
0 | 15 | 3029.860116 | 129.3315161 | 0.112873404 | 70.656984 | 71.38939712 | 0 | 0 | 0.3329631928 |  | 27.26874105 | 3.233287902 | 1.05985476 | 0.1128734039 | 4.994447892 | 1.638973689 | 8.185768684 | 40.92884342 | 128.5009148 | 642.5045741
0 | 20 | 3025.381604 | 129.1290564 | 0.109133239 | 68.21173781 | 71.28387465 | 0 | 0 | 0.3214402416 |  | 27.22843443 | 3.22822641 | 1.023176067 | 0.1091332389 | 4.821603624 | 1.584734057 | 7.640959472 | 38.20479736 | 128.3109744 | 641.5548719
0 | 25 | 3023.071163 | 129.2407766 | 0.10433444 | 65.21562413 | 71.22943619 | 0 | 0 | 0.3073213885 |  | 27.20764047 | 3.231019415 | 0.978234362 | 0.1043344402 | 4.609820827 | 1.513816905 | 6.978424696 | 34.89212348 | 128.2129851 | 641.0649257
0 | 30 | 3017.207396 | 129.0491381 | 0.098598831 | 61.52503951 | 71.09127443 | 0 | 0 | 0.2899299182 |  | 27.15486657 | 3.226228453 | 0.9228755927 | 0.09859883085 | 4.348948773 | 1.43027006 | 6.220171224 | 31.10085612 | 127.964294 | 639.8214699
0 | 35 | 3014.822766 | 129.1658014 | 0.091966549 | 57.38977917 | 71.0350879 | 0 | 0 | 0.2704429629 |  | 27.13340489 | 3.229145035 | 0.8608466875 | 0.0919665488 | 4.056644444 | 1.332932832 | 5.407234569 | 27.03617285 | 127.8631582 | 639.3157911
0 | 40 | 3009.292487 | 129.0832991 | 0.084389159 | 52.59614187 | 70.90478377 | 0 | 0 | 0.2478534794 |  | 27.08363238 | 3.227082478 | 0.788942128 | 0.08438915912 | 3.71780219 | 1.222376765 | 4.544555016 | 22.72277508 | 127.6286108 | 638.1430539
0 | 45 | 3006.847682 | 128.9939058 | 0.076375085 | 47.56549462 | 70.84717942 | 0 | 0 | 0.2241471127 |  | 27.06162914 | 3.224847645 | 0.7134824193 | 0.07637508497 | 3.36220669 | 1.106226554 | 3.71936232 | 18.5968116 | 127.524923 | 637.6246148
0 | 50 | 3002.529388 | 129.0217349 | 0.067728315 | 42.15463594 | 70.745432 | 0 | 0 | 0.1986490419 |  | 27.02276449 | 3.225543373 | 0.6323195391 | 0.06772831498 | 2.979735628 | 0.9801752233 | 2.920663035 | 14.60331517 | 127.3417776 | 636.708888
50 | 0 | 3060.036184 | 143.1018714 | 0.1481452983 | 98.0333425 | 72.10040396 | 0 | 0 | 0.4619712429 |  | 27.54032565 | 3.577546785 | 1.470500137 | 0.1481452983 | 6.929568643 | 2.055179465 | 14.24150718 | 71.20753589 | 129.7807271 | 648.9036356
50 | 5 | 3059.281033 | 142.9948771 | 0.1474731764 | 97.54004709 | 72.08261115 | 0 | 0 | 0.4596466431 |  | 27.5335293 | 3.574871927 | 1.463100706 | 0.1474731764 | 6.894699646 | 2.046368005 | 14.10909276 | 70.54546379 | 129.7487001 | 648.7435004
50 | 10 | 3062.410081 | 143.2106772 | 0.1453054126 | 96.2279345 | 72.1563376 | 0 | 0 | 0.4534634581 |  | 27.56169073 | 3.580266929 | 1.443419017 | 0.1453054126 | 6.801951872 | 2.015798048 | 13.71136131 | 68.55680654 | 129.8814077 | 649.4070384
50 | 15 | 3059.170035 | 143.3666402 | 0.141599501 | 93.77511063 | 72.07999582 | 0 | 0 | 0.441904798 |  | 27.53253032 | 3.584166005 | 1.406626659 | 0.141599501 | 6.628571969 | 1.962278892 | 13.00710686 | 65.0355343 | 129.7439925 | 648.7199623
50 | 20 | 3048.643722 | 143.0854886 | 0.1365699344 | 90.19993674 | 71.8319754 | 0 | 0 | 0.4250571879 |  | 27.4377935 | 3.577137215 | 1.352999051 | 0.1365699344 | 6.375857819 | 1.891175778 | 12.05786787 | 60.28933936 | 129.2975557 | 646.4877786
50 | 25 | 3047.754893 | 143.2630322 | 0.1304345417 | 86.18857582 | 71.81103285 | 0 | 0 | 0.4061540949 |  | 27.42979403 | 3.581575805 | 1.292828637 | 0.1304345417 | 6.092311424 | 1.804832157 | 10.99559957 | 54.97799785 | 129.2598591 | 646.2992957
50 | 30 | 3038.600832 | 143.0391694 | 0.1228008529 | 80.95910517 | 71.59534539 | 0 | 0 | 0.3815107951 |  | 27.34740749 | 3.575979236 | 1.214386578 | 0.1228008529 | 5.722661926 | 1.697977669 | 9.716952157 | 48.58476078 | 128.8716217 | 644.3581085
50 | 35 | 3034.139622 | 143.3003829 | 0.1143338603 | 75.39044788 | 71.49023061 | 0 | 0 | 0.3552691158 |  | 27.3072566 | 3.582509573 | 1.130856718 | 0.1143338603 | 5.329036737 | 1.578302438 | 8.410831673 | 42.05415836 | 128.6824151 | 643.4120755
50 | 40 | 3025.958914 | 143.0988603 | 0.1045202309 | 68.77806633 | 71.29747722 | 0 | 0 | 0.3241090019 |  | 27.23363023 | 3.577471508 | 1.031670995 | 0.1045202309 | 4.861635028 | 1.441899667 | 7.009989926 | 35.04994963 | 128.335459 | 641.677295
50 | 45 | 3021.174123 | 143.0240796 | 0.09395683638 | 61.76192792 | 71.18473822 | 0 | 0 | 0.2910462286 |  | 27.19056711 | 3.575601991 | 0.9264289189 | 0.09395683638 | 4.365693428 | 1.295486636 | 5.655697492 | 28.27848746 | 128.1325288 | 640.662644
50 | 50 | 3013.723446 | 142.7523153 | 0.08246063963 | 54.08663692 | 71.00918579 | 0 | 0 | 0.2548772718 |  | 27.12351102 | 3.568807883 | 0.8112995538 | 0.08246063963 | 3.823159077 | 1.136653443 | 4.34560693 | 21.72803465 | 127.8165344 | 639.0826721
3 | 0 | 2809.828733 | 126.2633395 | 0.09629319223 | 57.35537781 | 66.2050298 | 0 | 0 | 0.2702808503 |  | 25.2884586 | 3.156583489 | 0.8603306671 | 0.09629319223 | 4.054212755 | 1.362756078 | 5.524903074 | 27.62451537 | 119.1690536 | 595.8452682
3 | 3 | 2810.034256 | 126.1450742 | 0.0959015367 | 57.09742486 | 66.20987232 | 0 | 0 | 0.2690652757 |  | 25.29030831 | 3.153626855 | 0.8564613728 | 0.0959015367 | 4.035979136 | 1.357899036 | 5.480452176 | 27.40226088 | 119.1777702 | 595.8888509
3 | 6 | 2805.911405 | 125.8774335 | 0.09504329566 | 56.4849052 | 66.11272993 | 0 | 0 | 0.2661788448 |  | 25.25320265 | 3.146935838 | 0.847273578 | 0.09504329566 | 3.992682672 | 1.3461882 | 5.374902298 | 26.87451149 | 119.0029139 | 595.0145693
3 | 9 | 2806.594636 | 125.9720675 | 0.09392482223 | 55.84796539 | 66.12882818 | 0 | 0 | 0.2631773367 |  | 25.25935173 | 3.149301688 | 0.8377194809 | 0.09392482223 | 3.94766005 | 1.330008306 | 5.250420658 | 26.25210329 | 119.0318907 | 595.1594537
3 | 12 | 2806.685411 | 125.9881563 | 0.09227966115 | 54.87413912 | 66.130967 | 0 | 0 | 0.2585882885 |  | 25.2601687 | 3.149703907 | 0.8231120867 | 0.09227966115 | 3.878824327 | 1.306649944 | 5.06826559 | 25.34132795 | 119.0357406 | 595.178703
3 | 15 | 2808.986638 | 126.4320099 | 0.0903053356 | 53.81666345 | 66.18518839 | 0 | 0 | 0.2536050518 |  | 25.28087974 | 3.160800248 | 0.8072499517 | 0.0903053356 | 3.804075777 | 1.276970843 | 4.857693853 | 24.28846926 | 119.1333391 | 595.6666955
3 | 18 | 2800.786511 | 125.7704632 | 0.08743733122 | 51.89508489 | 65.99197744 | 0 | 0 | 0.2445498262 |  | 25.20707859 | 3.14426158 | 0.7784262734 | 0.08743733122 | 3.668247393 | 1.23785228 | 4.540748401 | 22.703742 | 118.7855594 | 593.927797
3 | 21 | 2803.003572 | 126.0101846 | 0.08457664598 | 50.26493299 | 66.04421572 | 0 | 0 | 0.2368679163 |  | 25.22703215 | 3.150254614 | 0.7539739949 | 0.08457664598 | 3.553018745 | 1.196687391 | 4.251852731 | 21.25926366 | 118.8795883 | 594.3979415
3 | 24 | 2804.859552 | 126.401671 | 0.08130761337 | 48.41313215 | 66.08794622 | 0 | 0 | 0.2281415104 |  | 25.24373597 | 3.160041774 | 0.7261969822 | 0.08130761337 | 3.422122657 | 1.149030668 | 3.932123883 | 19.66061941 | 118.9583032 | 594.791516
3 | 27 | 2800.087622 | 126.0859885 | 0.07741615024 | 45.99925475 | 65.97551027 | 0 | 0 | 0.2167663812 |  | 25.2007886 | 3.152149713 | 0.6899888213 | 0.07741615024 | 3.251495718 | 1.094473429 | 3.558675669 | 17.79337835 | 118.7559185 | 593.7795925
3 | 30 | 2797.7221 | 126.1757994 | 0.07334552935 | 43.57766606 | 65.91977397 | 0 | 0 | 0.2053549133 |  | 25.1794989 | 3.154394985 | 0.6536649909 | 0.07334552935 | 3.0803237 | 1.036117851 | 3.191578373 | 15.95789187 | 118.6555931 | 593.2779657
3 | 33 | 2802.483217 | 126.410888 | 0.0691440311 | 41.15460585 | 66.03195516 | 0 | 0 | 0.1939365111 |  | 25.22234896 | 3.160272201 | 0.6173190878 | 0.0691440311 | 2.909047667 | 0.9766865772 | 2.841227809 | 14.20613904 | 118.8575193 | 594.2875964
3 | 36 | 2800.904337 | 126.5898955 | 0.06477073869 | 38.56803466 | 65.99475367 | 0 | 0 | 0.1817475815 |  | 25.20813903 | 3.164747387 | 0.5785205199 | 0.06477073869 | 2.726213723 | 0.9140074218 | 2.491779576 | 12.45889788 | 118.7905566 | 593.952783
3 | 39 | 2797.007194 | 126.4633014 | 0.06027330862 | 35.84710447 | 65.9029294 | 0 | 0 | 0.1689255001 |  | 25.17306475 | 3.161582536 | 0.537706567 | 0.06027330862 | 2.533882501 | 0.8503756597 | 2.154752003 | 10.77376002 | 118.6252729 | 593.1263646
3 | 42 | 2791.326995 | 126.0462421 | 0.05559365891 | 32.97581722 | 65.76909286 | 0 | 0 | 0.1553948777 |  | 25.12194296 | 3.151156053 | 0.4946372583 | 0.05559365891 | 2.330923165 | 0.7848504644 | 1.829426129 | 9.147130644 | 118.3843672 | 591.9218358
3 | 45 | 2787.741918 | 126.1215949 | 0.05114947169 | 30.3292843 | 65.68462147 | 0 | 0 | 0.1429233851 |  | 25.08967726 | 3.153039873 | 0.4549392645 | 0.05114947169 | 2.143850777 | 0.7214296091 | 1.546637428 | 7.733187139 | 118.2323187 | 591.1615933
3 | 48 | 2783.594068 | 125.9084089 | 0.04667527689 | 27.63231188 | 65.58689005 | 0 | 0 | 0.130214202 |  | 25.05234661 | 3.147710223 | 0.4144846782 | 0.04667527689 | 1.95321303 | 0.6583907807 | 1.285977452 | 6.429887259 | 118.0564021 | 590.2820105
3 | 50 | 2790.63215 | 126.545573 | 0.04391585341 | 26.09733147 | 65.75272096 | 0 | 0 | 0.1229807772 |  | 25.11568935 | 3.163639325 | 0.391459972 | 0.04391585341 | 1.844711658 | 0.6186861583 | 1.141297569 | 5.706487845 | 118.3548977 | 591.7744886
6 | 0 | 2807.641889 | 126.0718024 | 0.09628109417 | 57.2823537 | 66.15350349 | 0 | 0 | 0.2699367324 |  | 25.268777 | 3.151795059 | 0.8592353056 | 0.09628109417 | 4.049050985 | 1.363088794 | 5.519216026 | 27.59608013 | 119.0763063 | 595.3815315
6 | 3 | 2812.144168 | 126.265189 | 0.09611567204 | 57.2736438 | 66.25958594 | 0 | 0 | 0.2698956879 |  | 25.30929751 | 3.156629725 | 0.859104657 | 0.09611567204 | 4.048435319 | 1.360794157 | 5.509087126 | 27.54543563 | 119.2672547 | 596.3362735
6 | 6 | 2812.785197 | 126.4941683 | 0.09551226658 | 56.97216025 | 66.27468982 | 0 | 0 | 0.2684749801 |  | 25.31506677 | 3.162354208 | 0.8545824037 | 0.09551226658 | 4.027124702 | 1.351180715 | 5.441373233 | 27.20686617 | 119.2944417 | 596.4722084
6 | 9 | 2809.147778 | 126.1780312 | 0.09426592549 | 56.12209856 | 66.18898516 | 0 | 0 | 0.2644691588 |  | 25.28233 | 3.154450779 | 0.8418314784 | 0.09426592549 | 3.967037382 | 1.334355071 | 5.293436446 | 26.46718223 | 119.1401733 | 595.7008665
6 | 12 | 2804.017065 | 126.0104881 | 0.09251268333 | 54.99142211 | 66.06809558 | 0 | 0 | 0.2591409716 |  | 25.23615358 | 3.150262203 | 0.8248713317 | 0.09251268333 | 3.887114574 | 1.309210597 | 5.08905159 | 25.44525795 | 118.922572 | 594.6128602
6 | 15 | 2809.131006 | 126.5141268 | 0.09049291097 | 53.94734384 | 66.18858999 | 0 | 0 | 0.2542208686 |  | 25.28217905 | 3.162853169 | 0.8092101576 | 0.09049291097 | 3.81331303 | 1.27924079 | 4.878145574 | 24.39072787 | 119.139462 | 595.6973099
6 | 18 | 2809.166886 | 126.5050592 | 0.08794185909 | 52.42499039 | 66.18943538 | 0 | 0 | 0.247046947 |  | 25.28250197 | 3.162626479 | 0.7863748559 | 0.08794185909 | 3.705704205 | 1.243230683 | 4.607045172 | 23.03522586 | 119.1409837 | 595.7049184
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

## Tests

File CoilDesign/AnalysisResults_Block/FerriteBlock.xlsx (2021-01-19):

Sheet: ydisp
 | N1 | 3 |  | I1 | 5 |  |  | f | 150000 | Q_2 | 5
 | N2 | 5 |  | I2 | 0 |  |  | w | 942477.7961
Xdisp | ydisp | Lpt_new (nH) | L_st (nH) | k_new (nH) | Mpt_st (nH) | VA_pt (VA) | VA_st (VA) | Po(W) | Vst |  | L_1 | L_2 | M_12 | k | Voc | Isc | Su | P_out | V_L_1 | VA_1
0 | 0 | 4322.804829 | 152.0505602 | 0.05855424598 | 129.3565826 | 1698.53543 | 1493.609322 | 93.26403604 | 2.489307736 |  | 38.90524346 | 3.801264005 | 1.94034874 | 0.1595554737 | 9.143678019 | 2.552241487 | 23.33687439 | 116.6843719 | 183.3366406 | 916.6832029
0 | 9 | 4277.06143 | 152.3381885 | 0.05369059206 | 127.6319204 | 1680.561733 | 1496.434727 | 85.14405256 | 2.456118741 |  | 38.49355287 | 3.808454713 | 1.914478807 | 0.158118311 | 9.021768832 | 2.513458805 | 22.67584431 | 113.3792216 | 181.3965944 | 906.9829719
0 | 18 | 4235.042531 | 152.6439215 | 0.04981544417 | 121.4974876 | 1664.051483 | 1499.437975 | 78.68856749 | 2.338069154 |  | 38.11538278 | 3.816098038 | 1.822462314 | 0.1511118951 | 8.588151327 | 2.387860972 | 20.50731138 | 102.5365569 | 179.6145098 | 898.072549
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

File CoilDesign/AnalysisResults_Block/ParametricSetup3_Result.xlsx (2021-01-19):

Variation | $X_displacement | $Y_displacement | Lpt_new: Freq(150kHz): None | L_st: Freq(150kHz): None | k_new: Freq(150kHz): None | Mpt_st: Freq(150kHz): None
1 | 45mm | 0mm | 4289.96730991778nH | 152.098220640302nH | 0.159917301 | 129.176796297209nH
2 | 45mm | 9mm | 4238.4621789577nH | 152.098246502401nH | 0.1586031779 | 127.343899477246nH
3 | 45mm | 18mm | 4195.08306488508nH | 151.794486805893nH | 0.1511930026 | 120.65073537449nH
4 | 45mm | 27mm | 4173.15116061046nH | 152.02110098009nH | 0.1391595513 | 110.840126969262nH
5 | 45mm | 36mm | 4122.06829780962nH | 150.610117040086nH | 0.1226853635 | 96.666817007936nH
6 | 45mm | 45mm | 4092.06619990368nH | 152.199778759675nH | 0.1032727747 | 81.5012335153076nH
7 | 45mm | 50mm | 4053.46179530416nH | 151.56906706569nH | 0.09128487402 | 71.5512378110547nH
8 | 36mm | 0mm | 4304.98758610384nH | 151.871305308883nH | 0.159598973 | 129.048781138941nH
9 | 36mm | 9mm | 4254.44302494556nH | 151.793903125776nH | 0.1580449793 | 127.007458026424nH
10 | 36mm | 18mm | 4211.95917254577nH | 152.187450983028nH | 0.1512329358 | 121.081524663001nH
11 | 36mm | 27mm | 4185.16705275605nH | 151.452610581679nH | 0.1386088399 | 110.353397689395nH
12 | 36mm | 36mm | 4147.40832447866nH | 151.555072494082nH | 0.122632531 | 97.2253079878479nH
13 | 36mm | 45mm | 4102.3118863879nH | 151.643080247614nH | 0.1030316062 | 81.2636091195098nH
14 | 36mm | 50mm | 4074.37777381379nH | 151.910272783981nH | 0.09106156713 | 71.6406205228031nH
15 | 27mm | 0mm | 4320.57934564092nH | 152.071598128354nH | 0.1594002887 | 129.206437245536nH
16 | 27mm | 9mm | 4266.24813167354nH | 151.970483970682nH | 0.1578498556 | 127.100385494345nH
17 | 27mm | 18mm | 4223.08709963601nH | 152.073422873577nH | 0.1508585237 | 120.895889066416nH
18 | 27mm | 27mm | 4197.23412073087nH | 152.13618634709nH | 0.1391948019 | 111.229728541607nH
19 | 27mm | 36mm | 4165.31861017094nH | 152.690656893912nH | 0.1230087826 | 98.0994258350536nH
20 | 27mm | 45mm | 4117.78473852265nH | 151.85344152798nH | 0.1029974942 | 81.4461947109074nH
21 | 27mm | 50mm | 4089.37077185653nH | 152.516090944504nH | 0.09078753484 | 71.6988683198158nH
22 | 18mm | 0mm | 4316.12418022302nH | 151.874536032772nH | 0.1596866055 | 129.287916492532nH
23 | 18mm | 9mm | 4271.46754499874nH | 152.366302260013nH | 0.1578643265 | 127.355299186161nH
24 | 18mm | 18mm | 4223.24159454995nH | 152.246138323112nH | 0.1510992288 | 121.159745896101nH
25 | 18mm | 27mm | 4193.76311959488nH | 151.568374789091nH | 0.1387455078 | 110.617840488313nH
26 | 18mm | 36mm | 4156.34339722555nH | 151.630469678666nH | 0.1224866125 | 97.2383486466553nH
27 | 18mm | 45mm | 4117.9223000692nH | 152.46878056142nH | 0.103312742 | 81.8622025558123nH
28 | 18mm | 50mm | 4085.51629224932nH | 152.188870034685nH | 0.09124429043 | 71.9483134100542nH
29 | 9mm | 0mm | 4321.93111849633nH | 152.461908608209nH | 0.1596910804 | 129.628428417667nH
30 | 9mm | 9mm | 4264.96142120233nH | 151.858647497795nH | 0.1580305926 | 127.179902033109nH
31 | 9mm | 18mm | 4221.98780342929nH | 151.944309655095nH | 0.1510164141 | 120.955288347157nH
32 | 9mm | 27mm | 4202.72595873601nH | 152.515652608344nH | 0.1388800161 | 111.189173782307nH
33 | 9mm | 36mm | 4163.04404606517nH | 152.090561193744nH | 0.1227593051 | 97.6812155619764nH
34 | 9mm | 45mm | 4117.12558988698nH | 151.933197721411nH | 0.1030340148 | 81.4899440072269nH
35 | 9mm | 50mm | 4074.79658075654nH | 151.22864681443nH | 0.09113072357 | 71.537674475284nH
36 | 0mm | 0mm | 4322.80482934679nH | 152.050560216694nH | 0.1595554737 | 129.356582649798nH
37 | 0mm | 9mm | 4277.06143047407nH | 152.338188518344nH | 0.158118311 | 127.631920443439nH
38 | 0mm | 18mm | 4235.04253138082nH | 152.643921510086nH | 0.1511118951 | 121.497487616088nH
39 | 0mm | 27mm | 4208.1975268403nH | 152.33181396786nH | 0.1388587575 | 111.177432412616nH
40 | 0mm | 36mm | 4176.04285976078nH | 152.507146367005nH | 0.1227207721 | 97.9367414445548nH
41 | 0mm | 45mm | 4124.37470033859nH | 152.701531300723nH | 0.1031971286 | 81.8970704092334nH
42 | 0mm | 50mm | 4091.42606658574nH | 152.529212470078nH | 0.09124816325 | 72.0838541137981nH

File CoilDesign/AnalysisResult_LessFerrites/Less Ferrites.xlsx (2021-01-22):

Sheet: ydisp
 | N1 | 3 |  | I1 | 5 |  |  | f | 150000 | Q_2 | 5
 | N2 | 5 |  | I2 | 0 |  |  | w | 942477.7961
Xdisp | ydisp | Lpt_new () | L_st () | k_nominal () | Mpt_st () | VA_pt (VA) | VA_st (VA) | Po(W) | Vst |  | L_1 (uH) | L_2(uH) | M_12 (uH) | k | Voc | Isc | Su | P_out | V_L_1 | VA_1
0 | 0 | 2687.021462 | 143.742834 | 0.1504090603 | 93.4765483 | 63.31145165 | 0 | 0 | 0.4404978561 |  | 24.18319316 | 3.593570851 | 1.402148224 | 0.1504090603
0 | 5 | 2690.378171 | 143.8346724 | 0.1495487486 | 93.02961912 | 63.39054223 | 0 | 0 | 0.438391752 |  | 24.21340354 | 3.595866811 | 1.395444287 | 0.1495487486 | 6.57587628 | 1.94034479 | 12.75946728 | 63.79733641 | 114.102976 | 570.51488
0 | 10 | 2685.538595 | 143.8715782 | 0.1474284691 | 91.63988989 | 63.2765124 | 0 | 0 | 0.4318428073 |  | 24.16984735 | 3.596789456 | 1.374598348 | 0.1474284691 | 6.477642109 | 1.910868519 | 12.37792239 | 61.88961193 | 113.8977223 | 569.4886116
0 | 15 | 2687.349751 | 144.2884386 | 0.1437166456 | 89.49214862 | 63.31918677 | 0 | 0 | 0.421721815 |  | 24.18614776 | 3.607210965 | 1.342382229 | 0.1437166456 | 6.325827225 | 1.86069271 | 11.7704206 | 58.85210301 | 113.9745362 | 569.872681
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

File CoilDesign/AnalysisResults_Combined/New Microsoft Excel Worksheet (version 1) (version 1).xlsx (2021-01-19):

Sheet: Sheet1
0

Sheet: Sheet2
In Gap Between ferrites
Middle
On Top of Ferrites

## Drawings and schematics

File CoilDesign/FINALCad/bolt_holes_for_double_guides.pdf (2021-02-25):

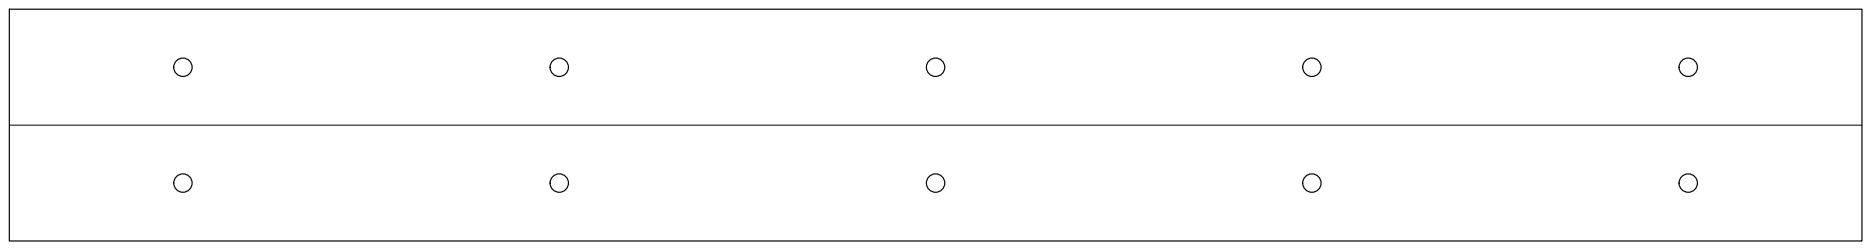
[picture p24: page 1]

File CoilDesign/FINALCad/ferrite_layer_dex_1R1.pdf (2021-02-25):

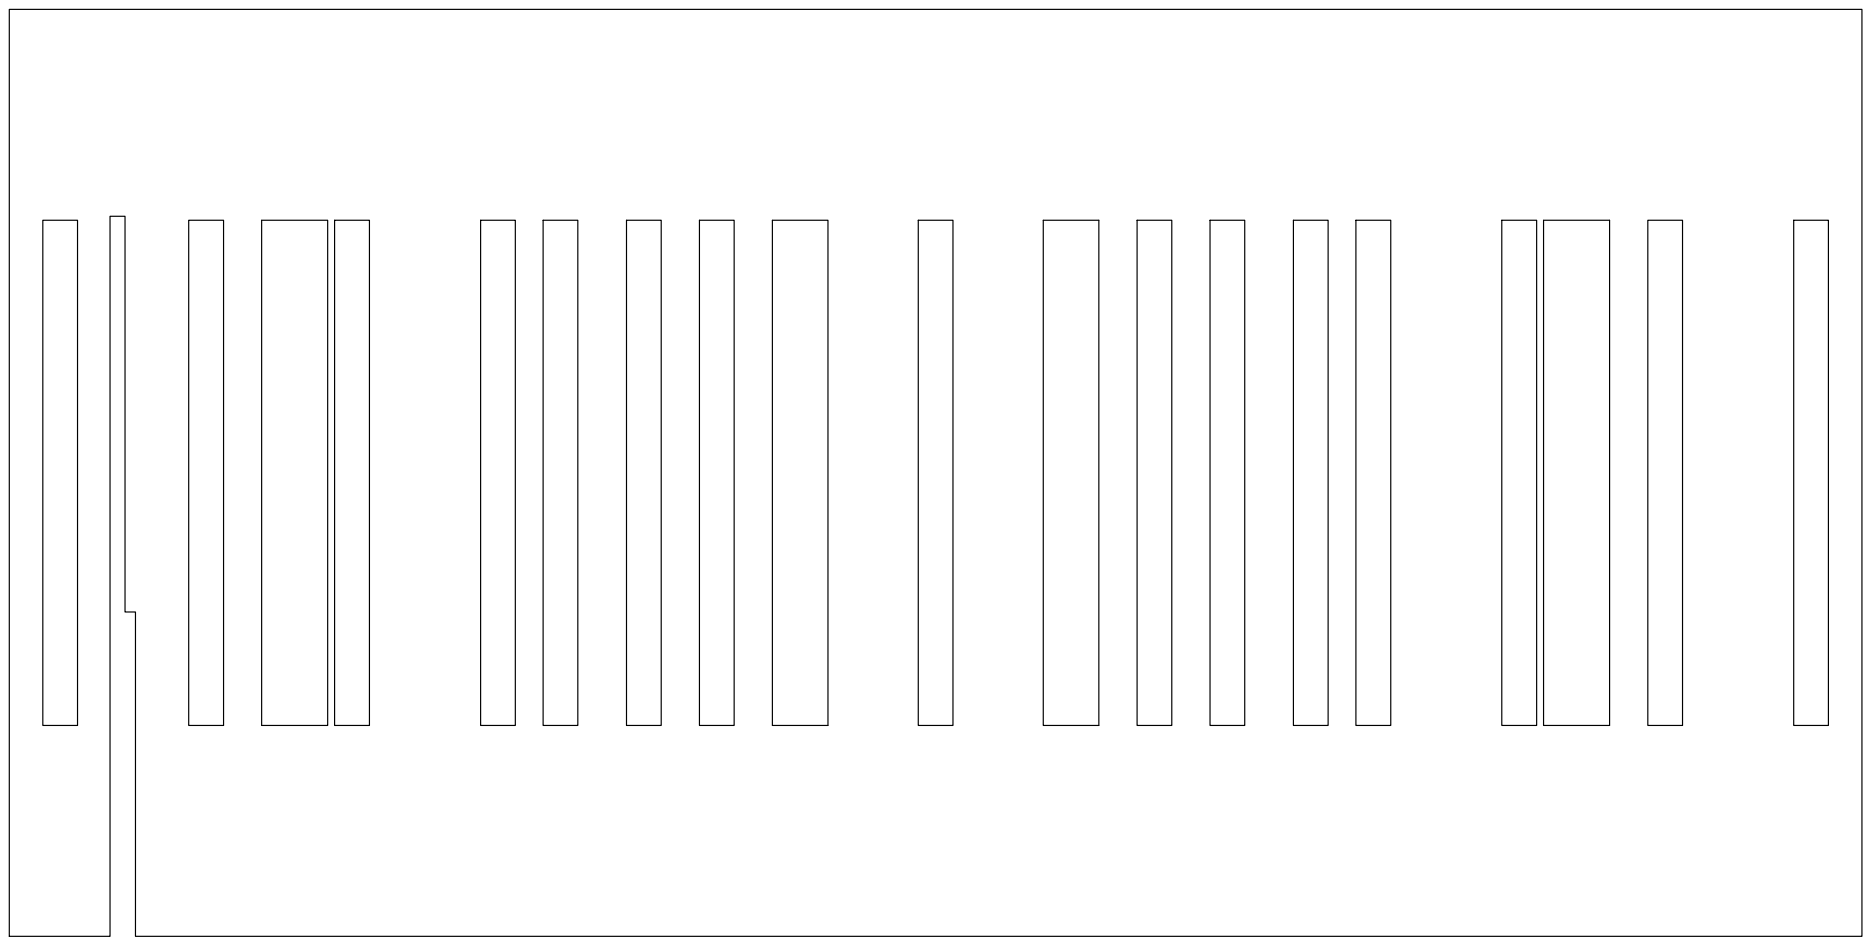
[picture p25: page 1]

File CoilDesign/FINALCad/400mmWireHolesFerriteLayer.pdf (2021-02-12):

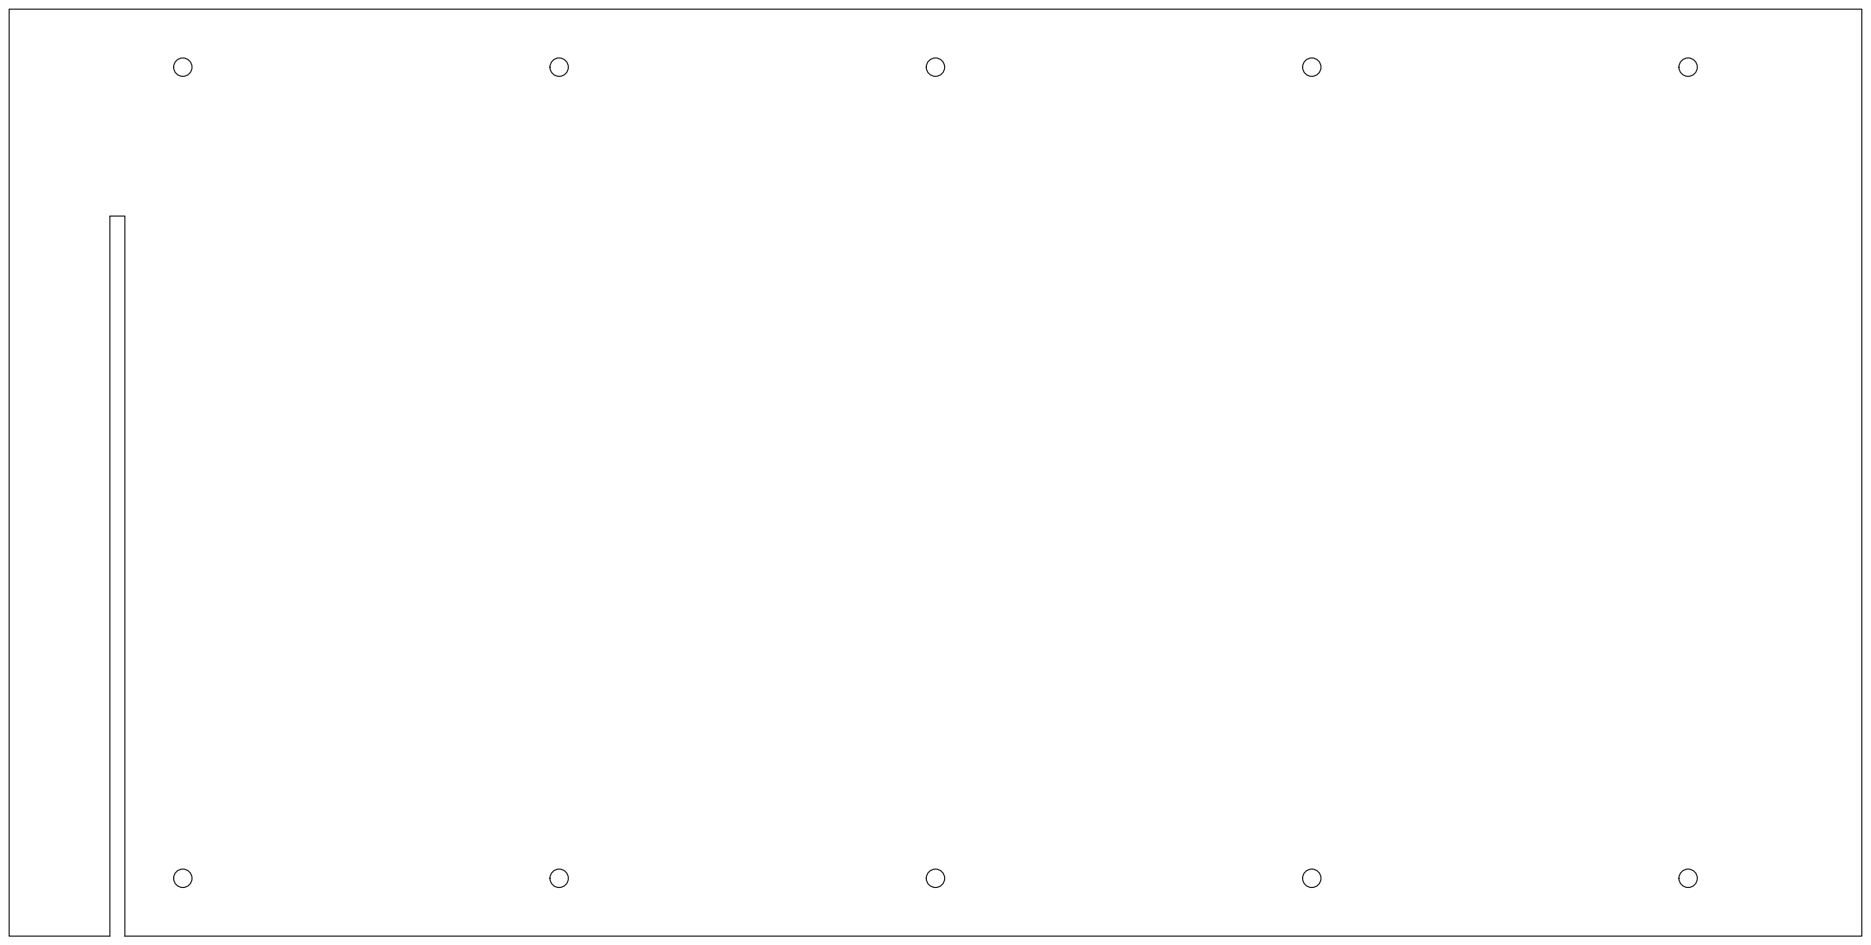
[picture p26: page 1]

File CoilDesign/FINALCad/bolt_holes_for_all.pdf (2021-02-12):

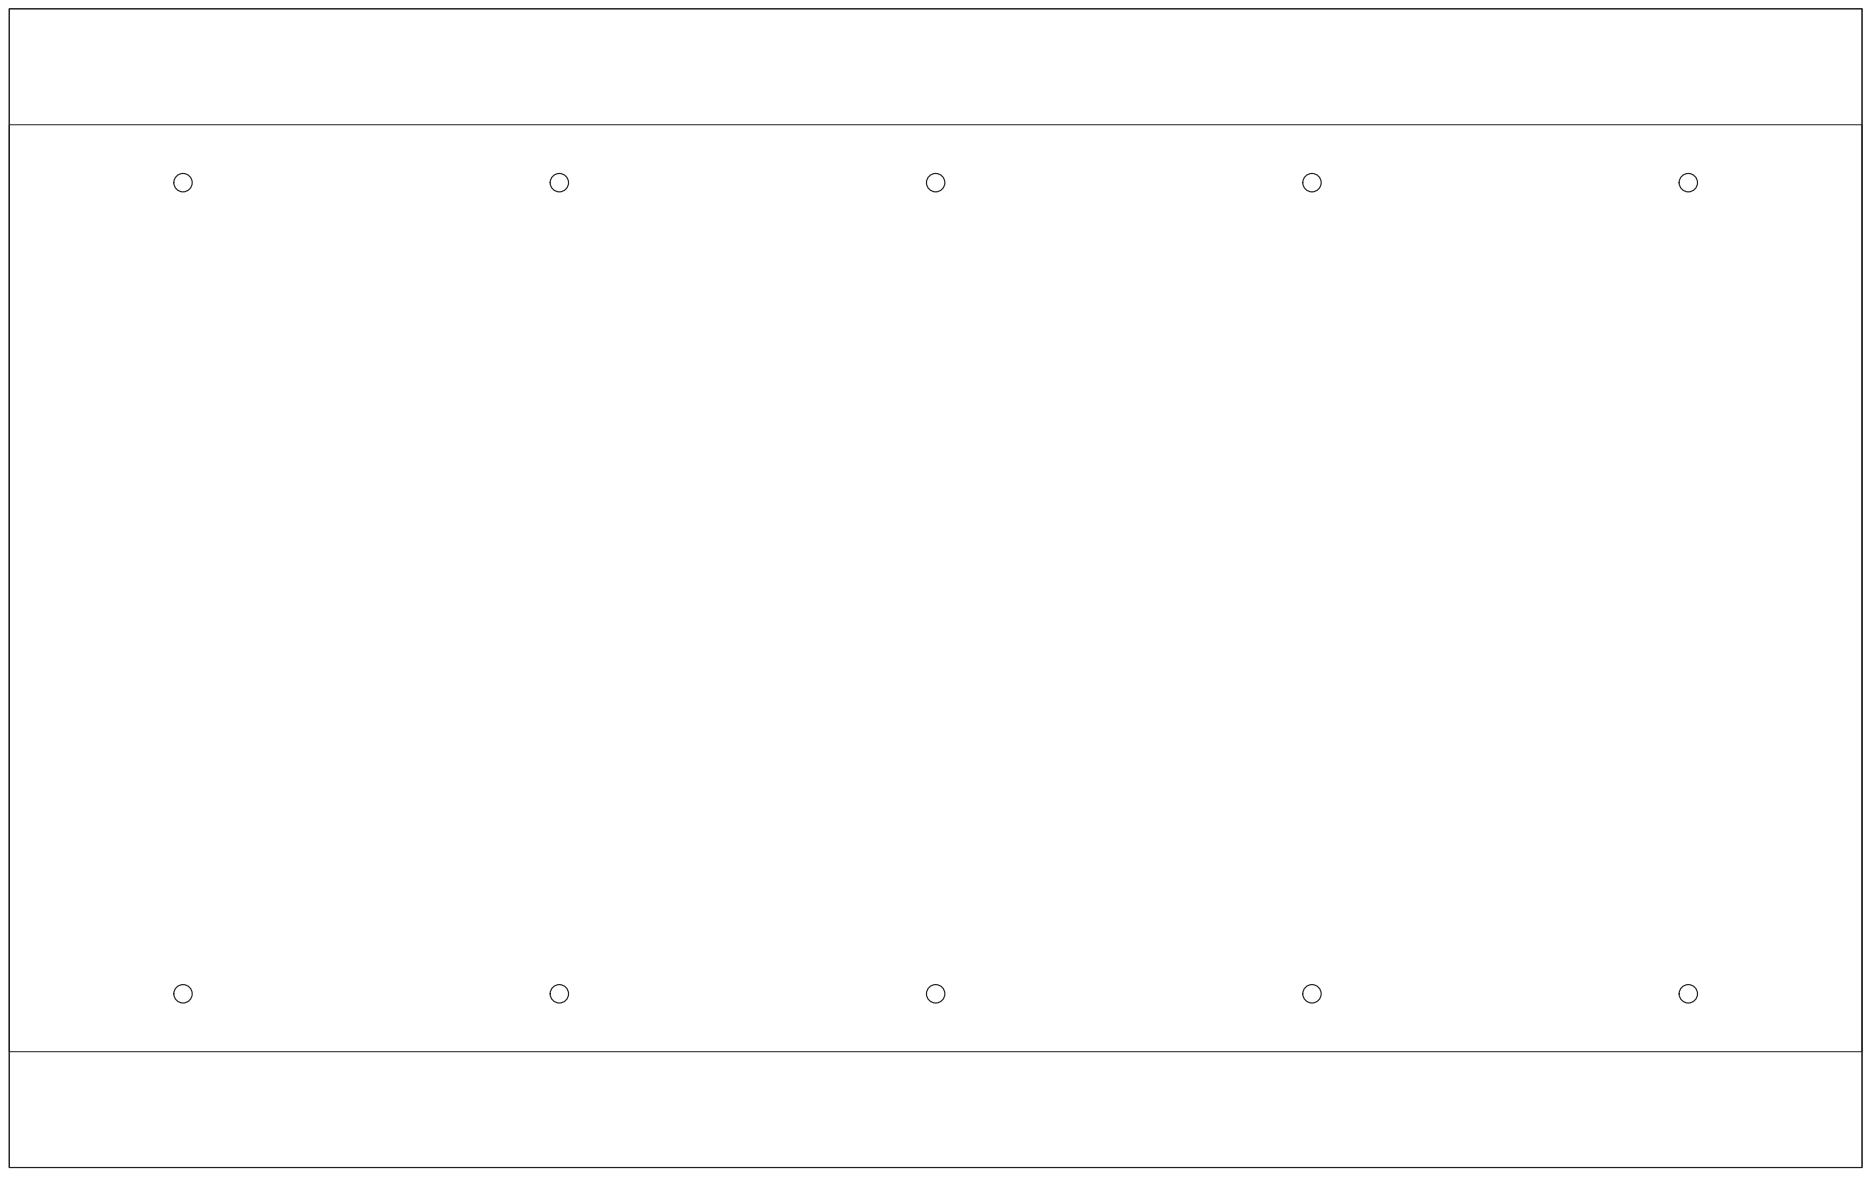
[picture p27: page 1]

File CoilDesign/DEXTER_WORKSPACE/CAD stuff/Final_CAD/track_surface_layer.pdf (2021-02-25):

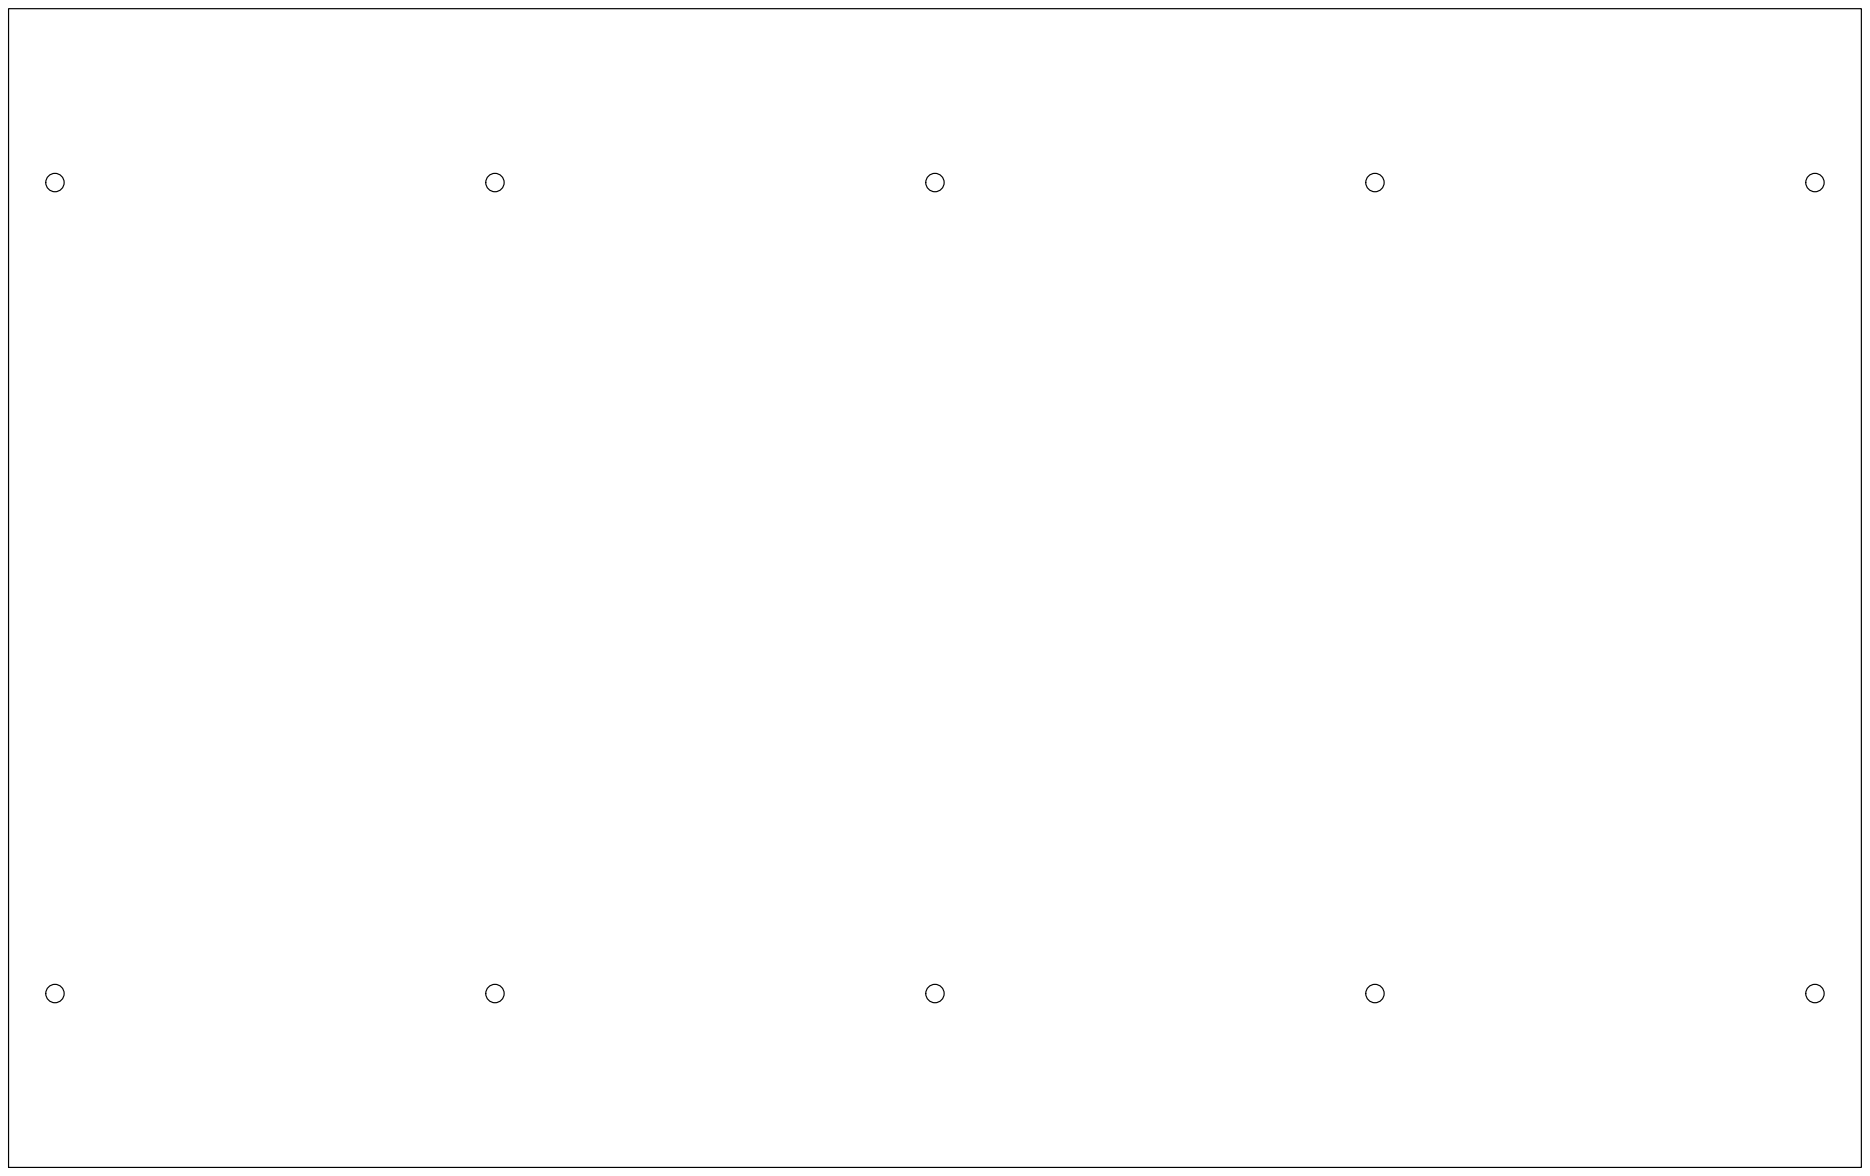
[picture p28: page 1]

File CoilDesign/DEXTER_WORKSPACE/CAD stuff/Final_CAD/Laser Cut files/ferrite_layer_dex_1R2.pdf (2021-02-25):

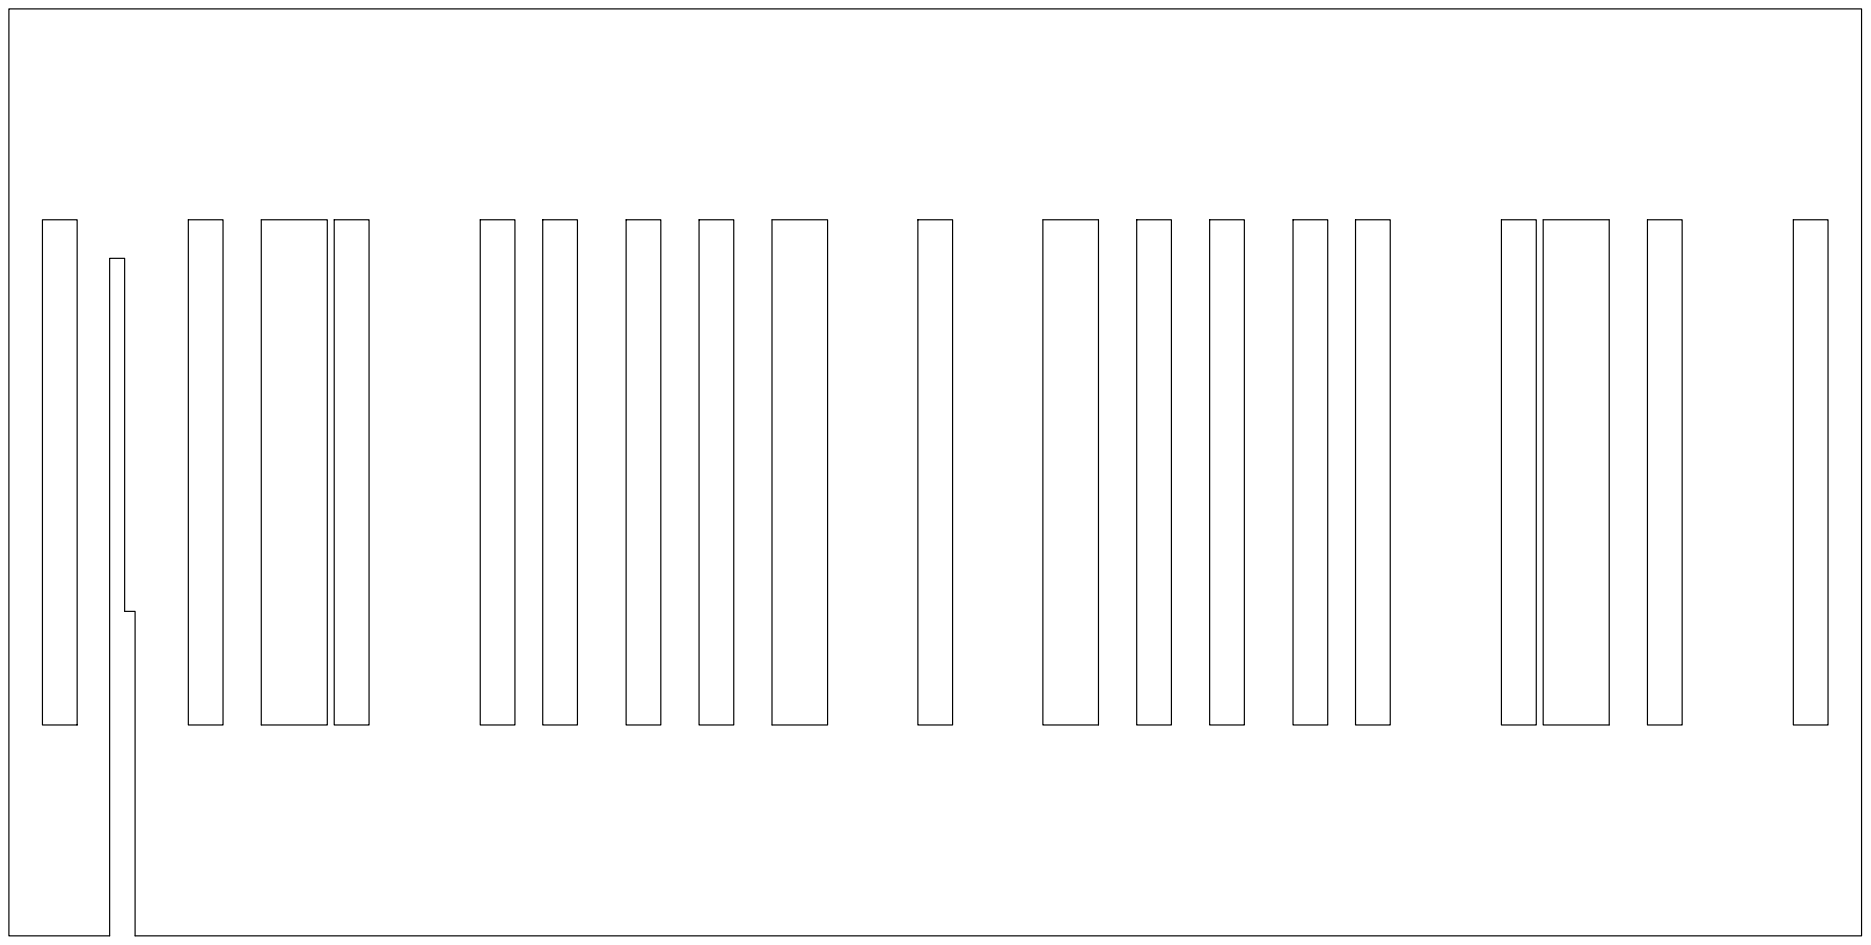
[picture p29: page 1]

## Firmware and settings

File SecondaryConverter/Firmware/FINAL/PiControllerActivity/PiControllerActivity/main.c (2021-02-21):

/*
 * PiControllerActivity.c
 *
 * Created: 18/01/2021 2:00:23 PM
 * Author : Manoj Kumaraguru
 */ 

#include <avr/io.h>
#include <avr/interrupt.h>
#include <stdbool.h>
#include "adc.h"
#include "timer.h"
#include "pwm.h"
#include "PI_Control.h"

int main(void)
{
	//Initialise modules and ports
	DDRC |= (1<<PORTC2);
	adcInit();
	timerInit();
	pwmInit();
	sei();

    while (1) 
    {
/*		//Check if error has been calculated
		
		if(returnErrorCalcFlag()) {
			cli(); 
			setPWM(returnOutput()); //Adjust pwm through PI controller
			setErrorCalcFlag(); //Reset flag
			sei();
		}*/
		//PINC ^= (1<<PORTC2); //debug led
    }
}

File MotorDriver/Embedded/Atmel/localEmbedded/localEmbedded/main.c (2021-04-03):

/*
 * localEmbedded.c
 *
 * Created: 9/12/2020 2:54:10 pm
 * Author : Earlene
 */ 

#include <avr/io.h>
#include "timer.h"
#include "Calculations.h"
#include "adc.h"
#include "uart.h"
#include "interrupt.h"
#include "global.h"
#include "watchdog.h"
#include "validate.h"

#define F_CPU 8000000
#include <util/delay.h>
#include <stdlib.h>
#include <string.h>
#include <avr/interrupt.h>
#include <stdbool.h>
#include <stdio.h>


int main(void)
{
// 	watchdog_init(); //initialize the watchdog timer (note: currently resulting in an error)

	//initialization functions
 	adc_init(); //initialize adc
 	stChangeInterrupt_init(); //initialize state change interrupt 
	encoderInterrupt_init();//initialize speed calculation interrupt
	uart_init(9600); //initialize uart at baud rate 9600
		
 	sei(); //turn on global interrupts
	  	
	//set output pins
	DDRD |= (1 << DDD3)|(1 << DDD5)|(1 << DDD4);
	DDRB |= (1 << DDB1);

	//set input pins
	DDRC &= ~(1 << DDC5) | ~(1 << DDC4) | ~(1 << DDC3); 
	DDRD &= ~(1 << DDD2); //INT0
	
	//initialize ADC/misc timer
	timer1_init(); // samples input voltage and current readings via ADC
	timer3_init(); // checks safety connection parameters (connection established & lost remote connection) and is a one second counter
 
	char transmitValue[10];
	
    while (1)
    {
		// 
 		if (arrayFull) {

			TCCR1B &= ~(1 << CS10) | ~(1 << CS11); // stop ADC sampling
			
 			convertVoltageAndCurrent();	// calculate voltage/current/power at H-Bridge and set over-voltage and over-current flags
			ramp(); // update the current speed requirement via a 10mV ramp
			updateDutyCycle(); // calculate on time for PWM waves
			
			TCCR1B |= (1 << CS10) | (1 << CS11); // restart ADC sampling
			
			GTCCR = ((1<<TSM)|(1<<PSRASY)|(1<<PSRSYNC));  //stop all timers
			
			//re-initialize PWM timers
			timer0_init(returnFinalPeriod(),returnLeftOnTime());  // set values for PWM that controls the left FET driver
			timer2_init(returnFinalPeriod(),returnRightOnTime());  // set values PWM that controls the right FET driver

			TCNT0 = 0; // setting offset for left PWM
			TCNT2 = 0; // setting offset for right PWM
			
			GTCCR = 0; // start timers
			 		
 			//checkADC(); //stops the ADC interrupt (i.e., sampling) and prints out current/voltage values. Uses a 500ms delay (but no sampling is happening in this time).
			 
			arrayFull = false;

 		}
		 
		 if(oneSecCounter >= 25){//run every second
			 
			//calculate car speed and restart one second counter
			PORTD ^= (1 << DDD4);
			realSpeedCalc();
			rotCount = 0;
			oneSecCounter = 0;		 
		 }
		 
		 
		if (sendData) {//every 1s. Note that checkADC and checkInterrupt can't run simultaneously due to the 500 ms delay in checkADC.

			//stop ADC sampling
			TCCR1B &= ~(1 << CS10) | ~(1 << CS11);
			
			//checkInterrupt();
			
			// calculate the average voltage and current over the last second 
			averageVoltageAndCurrent();
			
			//checkTransmission();
			
			// send calculation values through uart 
			checkAvgCalc();
			sendData = false;
			
			// restart ADC sampling
			TCCR1B |= (1 << CS10) | (1 << CS11);
			
		}
    }
}

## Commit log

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2020-12-01 MotorDriver\\Hardware: Rough outline of draft
    Very rough outline of possible circuit, pending component decisions and further modelling.
    [ConverterSch_Draft.SchDoc]
2020-12-01 Revert "Update ConverterSch_Draft.SchDoc"
    This reverts commit 2e248e288a3160e9a3f66f64bf948bdd53f6f13e.
    [ConverterSch_Draft.SchDoc]
2020-12-01 MotorDriver\\Hardware: Minor work on library
    Minor work on setting up library, prepping for schematic design.
    [ConverterSch_Draft.SchDoc, IRS21814STRPBF_CUSTOM.SchLib]
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2020-12-03 Steering\\Hardware: H-Bridge Driver.IntLib and First draft of Steering Controller
    Bluetooth module missing and need to decide on uC supply voltage
    [ConverterSch.SchDoc]
2020-12-03 MotorDriver\\Hardware: First draft schematic has been outlined
    Placeholders still present, and values not calculated (need to simulate in LTSpice).
    [ConverterSch.SchDoc]
2020-12-03 Added first draft of RemoteController schematic
    Created skeleton structure for schematic, used generic Altium components for everything except the MCU, ISP header and the clock crystal
    [RemoteSch.SchDoc]
2020-12-05 Updated SteeringController and RemoteController schematics
    Need to decide on a bluetooth module and the way speed will be transmitted to the other embedded team.
    [ConverterSch.SchDoc, RemoteSch.SchDoc, Steering_Converter.PrjPcb]
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2020-12-07 MotorDriver\\Hardware: Rehomed a poor little lost library :cry:
    Sorry SecondaryConverter team, all fixed.
    [ConverterSch.SchDoc, SumWkshop.PcbLib, SumWkshop.SchLib]
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2020-12-07 MotorDriver\\Hardware: Updated and finalised first draft of schematic, pending review.
    Izzy (+embedded team?) will review, then meeting on tues 8/12 for formal review.
    [ConverterSch.SchDoc, Motor_Driver.PrjPcb]
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2020-12-07 PCB file got lost so now i'm uploading it to the right place
    [SumWkshop.PcbLib]
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2020-12-07 i hate how absolutely everyone can see me be stupid live on slack
    [SumWkshop.PcbLib]
2020-12-07 Updated RemoteController schematic
    Added Bluetooth module, proper acceleration signals to ADC channels,
    3.3V regulated power supply with reverse-voltage protection, 6 pin
    single row header for acceleration switches, and decoupling caps for MCU
    and BLE.
    [RemoteSch.SchDoc]
2020-12-07 Primary Converter schematic draft v1.1
    Added new library for extra parts (currently contains MOSFET & DC-DC converter) & started sorting decoupling caps. Still requires ISP header & validation of diodes
    [ConverterSch-draft.SchDoc, Primary_Converter.PrjPcb]
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2020-12-07 Fixed erroneous pin order in ACS70331 footprint
    [SumWkshop.PcbLib, SumWkshop.SchLib]
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2020-12-07 General cleanup for presentation
    Edited title block, added defined areas, and cleaned up/assigned decoupling capacitors
    [ConverterSch-draft.SchDoc, Primary_Converter.PrjPcb]
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2020-12-08 Fixed diode
    [ConverterSch-draft.SchDoc]
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2020-12-08 Added second converter schematic to project
    Added second converter schematic file to Altium project
    [ConverterSch_2ndDriver.SchDoc, Steering_Converter.PrjPcb]
2020-12-08 MotorDriver\\Hardware: Making changes post-review
    Removed excess filters, added MCU, fixed drivers, fixed motor capacitors.
    [ConverterSch.SchDoc, Motor_Driver.PrjPcb]
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2020-12-08 MotorDriver\\Hardware: Further updates to draft post-review
    TODO:
    - MCU linkages
    - Update drivers
    - Power capacitor layouts from datasheet
    - High power resistor for linear regulator.
    [ConverterSch.SchDoc]
2020-12-08 Testing Commit - Fixed Grid Dimensions Pt.2
    [ConverterSch.SchDoc]
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2020-12-08 Updated library & fixed alignment issues
    Added IRS21834 FET Driver & SRH05 DC-DC Converter to library. Fixed alignment of MOSFET from library. Changed gridsize to 100mil & aligned components. Swapped in IRS21834 into schematic, using pin choices from Andrey.
    [ConverterSch-draft.SchDoc, PrimaryConverterSch-draft.SchDoc, [Team_01] - Primary_Converter.PrjPcb]
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2020-12-08 Fixed schematic alignnment/grid settings
    Changed all settings to 100mil
    [RemoteSch_V2.SchDoc]
2020-12-08 Fixed snap distance setting
    [RemoteSch_V2.SchDoc]
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2020-12-08 Some fixes to the circuit
    [embeddedCircuit.SchDoc]
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2020-12-09 Fixed Grid and Filename
    [Steering_Converter_DRV8833C.SchDoc, Steering_Converter_OG.SchDoc, Steering_Converter_ZXBM5210.SchDoc]
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2020-12-09 Revert "Merge branch 'main' of https://github.com/UoAPEGroup/2020-srw-rc-car into main"
    This reverts commit 4ed618d14d167cb02b91ed726031070c73679120, reversing
    changes made to a0dfabedbd6f4372dbaf4d0a0b7591951f594f26.
    [Steering_Converter.PrjPcb, Steering_Converter_ZXBM5210.SchDoc]
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2020-12-09 update files
    This reverts commit 28ab24ed1fe59d5a2b9f71fb381fabf39ca966fc.
    [Steering_Converter.PrjPcb, Steering_Converter_ZXBM5210.SchDoc]
2020-12-09 Fixed PWM test firmware
    [main.c]
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2020-12-09 BLE Module Via Stitching Complete
    Need to update design rules and pour the layers
    [BLE_Module_Latest.PcbDoc, BLE_Module_Vias.PcbDoc, Bluetooth_Module.PrjPcb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]
2020-12-09 Adding missing connection and cleaning up BLE Module folder
    [BLE_Module.PcbDoc, BLE_Module_Latest.PcbDoc, BLE_Module_Vias.PcbDoc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]
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2020-12-10 Updated RC Schematic for first PCB revision
    Added R/C values, Accel switch capacitors, debugWire header, and deleted
    BLE module from this PCB
    [RemoteSch_V2.SchDoc]
2020-12-10 Added PCB components, edited board shape
    Added BLE PCB headers, changed some nets, started adding components to
    PCB
    [RemoteCntrl.PcbDoc, RemoteSch_V2.SchDoc]
2020-12-10 BLE Module PCB Update - Poured Planes, increased track width and min clearance
    [BLE_Module_Latest.PcbDoc, Bluetooth_Module.PrjPcb, Bluetooth_Module_V1.SchDoc]
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2020-12-10 MotorDriver\\Hardware: Work on PCB, error fixing
    [ConverterSch.SchDoc, MotorDriverPCB.PcbDoc]
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2020-12-11 Added some short cct regulator designs
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2020-12-12 Added EE209 Library file
    Had an issue with Test points not being added to PCB doc properly
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2020-12-13 Design rule & Switching layout
    Added design rules to comply with default PCBWay requirements. Reconfigured switching setup and began setting out the drivers and MOSFETS so that routing can be done.
    [Extra-ECSESummer-Footprints.PcbLib, Extra-ECSESummer-Schematics.SchLib, PrimaryConverterSch-PCB.PcbDoc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]
2020-12-13 MotorDriver\\Hardware: Integrating PCB modules into a cohesive layout
    Tracks and vias
    MCU set up
    Resolve U4 OPAMP component issue
    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
    [ConverterSch.SchDoc, MotorDriverPCB.PcbDoc]
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2020-12-13 Fixes from review
    Replaced fet, fixed driver footprint, moved sensor in schematic, & fixed GND labels
    [Extra-ECSESummer-Footprints.PcbLib, Extra-ECSESummer-Schematics.SchLib, PrimaryConverterSch-PCB.PcbDoc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]
2020-12-13 Added rough layout of PCB for remote controller
    Added traces and pours for planes, need to maybe find better orientation
    for MCU to shorten trace lengths and routing.:
    [RemoteCntrl_1R1.PcbDoc, RemoteSch_1R1.SchDoc, Remote_Controller.PrjPcb]
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2020-12-14 Layout & Connecting
    Begun layout of FET and input connections including 12V plane
    [PrimaryConverterSch-PCB.PcbDoc]
2020-12-14 Replaced all Capacitors with 0805's and Updated PCB
    [BLE_Module_USB_Header.PcbDoc, Bluetooth_Module_V1.SchDoc]
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2020-12-14 Solved timer offset issue
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2020-12-14 Moved MCU to right side of board
    BLE Rx and Tx traces were too long on left side, too much noise
    [RemoteCntrl_1R2.PcbDoc, RemoteSch_1R1.SchDoc]
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2020-12-14 Fixed missing connection in Steering Controller PCB
    [Steering_Converter_ZXBM5210.PcbDoc]
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2020-12-14 Test FET Reconfig
    Connected MOSFETS with drivers & compensating inductors, keeping new design points in mind
    Note both FETS need 3 caps in outer loop each, & ask about smaller loop caps.
    [PrimaryConverterSch-PCB.PcbDoc]
2020-12-15 Continuation of MOSFET setup
    Added output loop caps and began routing of control signals and bootstrap traces
    [PrimaryConverterSch-PCB.PcbDoc, PrimaryConverterSch-draft.SchDoc]
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2020-12-15 Edited RC PCB and Schematic
    Added 9V and GND planes for power connection, changed MCU pins used for
    RTS and CTS, addeed status LED, added filters for output of direction switches, added HM10 header.
    [RemoteCntrl_1R2.PcbDoc, RemoteSch_1R1.SchDoc]
2020-12-15 Added Filter stage for pot.
    Added RC Filter for steering potentiometer at input to MCU
    [RemoteSch_1R1.SchDoc]
2020-12-15 Added components to PCB and changed MCU input pin
    Changed MCU input net to filter output and added RC filter to PCB
    [RemoteCntrl_1R2.PcbDoc, RemoteSch_1R1.SchDoc]
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2020-12-15 More routing
    Connected driver control signals and finished off a couple of the grounds
    [PrimaryConverterSch-PCB.PcbDoc]
2020-12-15 Edited PCB and Sch for RC
    Added traces and main polygon planes, edited MCU pins used for Accel.
    pins, still unsure on how 5V ISP and 3V3 MCU Power Supply works
    [RemoteCntrl_1R2.PcbDoc, RemoteSch_1R1.SchDoc]
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2020-12-16 Added Design rules for polygons and added traces for most connections
    Removed some reliance on polygon pours and ensured connections were made before pouring, might have some more to check on top side of MCU
    [RemoteCntrl_1R2.PcbDoc]
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2020-12-16 Replaced the boost inductor model with a efd20.
    [IPT_Secondary_Converter.SchDoc]
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2020-12-17 Remote Controller Switches correctly placed + other updates
    Alignment of the Forward and Reverse Switches with the Remote Controller Case.
    [Bluetooth_Module_1R0.PrjPcb, RemoteCntrl_1R2.PcbDoc, Remote_Controller.xls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]
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2020-12-17 Fixed thermistor headers
    [PrimaryConverterSch-PCB.PcbDoc, PrimaryConverterSch-draft.SchDoc]
2020-12-17 Fixed PCB size
    [MotorDriver_Experimental.PcbDoc]
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2020-12-19 Fixed ground issues
    [PrimaryConverterSch-PCB.PcbDoc]
2020-12-19 Fixed board sizing
    [PrimaryConverterSch-PCB.PcbDoc]
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2020-12-22 MotorDriver\\Hardware: Fixed broken connections and polygon pours in PCB
    [MotorDriver_1R1.PrjPcb, MotorDriver_Experimental.PcbDoc]
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2021-01-08 MotorDriver\\Hardware: Improved paths for 3V3 and Vin
    Rearranged zener diode to no longer block primary Vin path, and fleshed out Vinfilt connections as it feeds all 3V3 and 12V
    [MotorDriver_1R1.PrjPcb, MotorDriver_Final_V1.0.PcbDoc]
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2021-01-10 Remote Controller: Error checked and "physically" tested pcb size
    [BLE_Module_1R1.PcbDoc, RemoteCntrl_1R3.PcbDoc, Steering_Converter_1R2.PcbDoc]
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2021-01-10 MotorDriver\\Hardware: Improved GND connections, fixed pours
    [MotorDriver_Final_V1.0.PcbDoc, Steering_Converter.PrjPcb]
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2021-01-11 Fixing variable overflow somewhere...
    [adc.c, main.c]
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2021-01-11 MotorDriver\\Hardware: Resolved solder mask sliver issues, polished PCB, pending final review
    In addition to repositions the rule was also changed to 7.5mm, so that adjacent pads *within* a component no longer conflicted.
    [MotorDriver.SchDoc, MotorDriver_Final_V1.0.PcbDoc]
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2021-01-12 Fixed the Crystal.
    [IPT_Secondary_Converter.PcbDoc, IPT_Secondary_Converter.SchDoc]
2021-01-12 Issues with timer 3 - change to fast PWM
    [main.c, usart0.c]
2021-01-12 MotorDriver\\Hardware: PCB fixes made; unpolished
    unrouted net warning is false, current path jumps two polygons to source
    [MotorDriver.SchDoc, MotorDriver_Final_V1.0.PcbDoc]
2021-01-12 MotorDriver\\Hardware: Rearranged current sensor (vulnerable to noise?)
    [MotorDriver_Final_V1.0.PcbDoc]
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2021-01-12 Reverted timer1 OCR1B change due to an interrupt trigger error
2021-01-12 Update Excel Files
    Error with old files being restored somehow, updated to latest version
    [New Microsoft Excel Worksheet.xlsx, Output Variables Table 1.xlsx, ParametricSetup2_Result.xlsx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]
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2021-01-13 Firmware: Cleaned up receiver logic, reverted back to enigma code
    [main.c]
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2021-01-13 Fixed timer3 issue, usart0 comms now triggered on timer3
    [usart0.c]
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2021-01-13 MotorDriver\\Hardware: PCB final tweaks
    - driver now has decoupling 12V->GND
    - current sensor on underside and away from noise
    - mounting vias added
    [MotorDriver.SchDoc, MotorDriver_Final_V1.0.PcbDoc]
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2021-01-15 Re-arranging and Fixing up sch
    [IPT_Secondary_Converter.SchDoc]
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2021-01-15 Fixed up Test Points - Saving work
    [IPT_Secondary_Converter.PcbDoc, IPT_Secondary_Converter.SchDoc]
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2021-01-15 Fixed C9 & Worked on PCB
    [IPT_Secondary_Converter.PcbDoc, IPT_Secondary_Converter.SchDoc]
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2021-01-18 Updated the Design Rules and fixed up the board
    [IPT_Secondary_Converter.PcbDoc, IPT_Secondary_Converter.SchDoc]
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2021-01-20 CoilDesign\\DEXTER_WORKSPACE\\EXPERIMENTS\\individual_wires_0r2: Got electrocuted.... Current leak to the air
    _ Saving works
    _ Boundary bugs
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2021-01-20 Implemented RESET and HALT commands, added timer_control_halt to stop all timers: PWM, ADC etc.
    [main.c, usart0.c]
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2021-01-22 MotorDriver\\Embedded: Bugfixing, timing issue unresolved
    [main.c]
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2021-01-22 Removed 5V Reg, Inductor Symbol, Fixed the layout & Updaed PCB - Saving Work
    [IPT_Secondary_Converter.PcbDoc, IPT_Secondary_Converter.SchDoc]
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2021-01-24 Fixed the pins the the Totem & Boost, also worked on the sldies - Saving Work
    [IPT_Secondary_Converter.SchDoc]
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2021-01-26 Fixed BJT & Totem Pole Wiring, & worked on PCB, - Saving Work
    [IPT_Secondary_Converter.PcbDoc, IPT_Secondary_Converter.SchDoc]
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2021-01-26 Fixed fet model in Spice schematic
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2021-01-27 Arranged Caps on the PCB and fixed pours - Saving work
    [IPT_Secondary_Converter.PcbDoc]
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2021-01-27 Firmware: Fixed PI Controller Limit bug + cleaned up code
    [main.c]
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2021-01-27 Fixing ADC
2021-01-27 Fixed ADC, working on accuracy and safety cut off
    [adc.c, adc.h]
2021-01-28 Ran Design Rule Check - Need to fix a few parts. - Changed min hole size to 0.4mm
2021-01-28 DRC done - All relevant errors fixed - Saving work.
    [IPT_Secondary_Converter.PcbDoc]
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2021-01-28 PNP was incorrectly connected. - Fixed on sch & PCB. - DRC done - Saving Work
    [IPT_Secondary_Converter.PcbDoc, IPT_Secondary_Converter.SchDoc]
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2021-01-28 Fixing io pin ddr
    [main.c]
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2021-02-01 Fixed other ascii chars being recognised as digits for duty cycle, amended halt msg, capped max duty at 99%, implemented ramp down at reset and halt
    [adc.h, main.c, usart0.c]
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2021-02-02 Created schematic for bjts and replaced them in converter schematic
    [BJTsECE.SchLib, IPT_Secondary_Converter.SchDoc]
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2021-02-02 Fixed safety parameter error
    [Calculations.c, interrupt.c, validate.c]
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2021-02-03 Changed Via placement with silk screen issues
    [RemoteCntrl_1R3.PcbDoc]
2021-02-03 Fixed the transistor issue, Fixed up the sch, compared to ltspice, finalised sch - Saving work, ready for PCB
    [BJTsECE.SchLib, IPT_Secondary_Converter.PcbDoc, IPT_Secondary_Converter.SchDoc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]
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2021-02-03 Replace the Caps in Boost Conv
    [IPT_Secondary_Converter.SchDoc, UCD1E221MNL1GS.PcbLib, UCD1E221MNL1GS.SchLib]
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2021-02-04 Fixed all designators - Saving Work
    [IPT_Secondary_Converter.PcbDoc]
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2021-02-04 DRC done, fixed all relevant errors - Saving Work
    [IPT_Secondary_Converter.PcbDoc]
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2021-02-09 Fixed ADC
2021-02-09 Fixed proteus schematic
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2021-02-09 Adjusted pwm calculation and error calculation algorithm
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2021-02-10 Added resetting timer int flag
    [adc.c]
2021-02-10 Firmware: Steering calibration fixed
    [main.c]
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2021-02-11 Revert "update python_script"
    This reverts commit cefd84faedf37b4a1e4e13bfd03803f917a28817.
    [main.c, usart0.c]
2021-02-11 Voltage protection is working correctly now
    [adc.c, adc.h, usart0.c]
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2021-02-11 ADC, Steering+Accel read code updates
    Added get ADC functions and Steering+accel functions to avoid global
    variable usage.
    [adc.c, adc.h, main.c]
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2021-02-12 Updated firmware with correct values for thermistors, waiting for current sensor
    [adc.c, adc.h, usart0.c]
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2021-02-13 CoilDesign\\DEXTER_WORKSPACE\\CAD stuff\\Final_CAD: Added track_walls and resolved some links
    [IPT_TRACK_assembly.0007.iam, IPT_TRACK_assembly.0008.iam, IPT_TRACK_assembly.iam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]
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2021-02-19 Removed error calculation polling and directly calls setpwm
    [adc.c, main.c]
2021-02-19 Firmware: Fixed steering pi controller bug
2021-02-21 CoilDesign\\DEXTER_WORKSPACE\\CAD stuff\\Final_CAD: Deleted excel link --- for some reason the OLE link still persisted after breaking the link --- solved
    [ferrite_layer_dex_1R1.0012.ipt, ferrite_layer_dex_1R1.0013.ipt, ferrite_layer_dex_1R1.ipt]
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2021-02-22 CoilDesign\\DEXTER_WORKSPACE\\CAD stuff\\Final_CAD: Reverted back to the original plan, all parameters are controlled by an excel file --- Can't check this --- Inventor hates Onedrive :(
    [IPT_TRACK_assembly.0013.iam, IPT_TRACK_assembly.0017.iam, IPT_TRACK_assembly.iam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]
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2021-02-25 CoilDesign\\DEXTER_WORKSPACE\\CAD stuff\\Final_CAD\\ some where in my folder idk: Updated ferrite_layer with the correct dimensions, fixed dimensions in the excel file, added some Engraving templates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
    [IPT_TRACK_assembly.0017.iam, IPT_TRACK_assembly.0018.iam, IPT_TRACK_assembly.iam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]
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
